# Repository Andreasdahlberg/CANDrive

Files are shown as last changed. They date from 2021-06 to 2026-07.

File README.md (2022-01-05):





# CANDrive
CANDrive is a brushed DC Motor Controller controlled via a [CAN](https://en.wikipedia.org/wiki/CAN_bus) interface.

## Features

* Velocity control
* Torque control
* CAN interface
* Firmware updates over CAN
* Emergency stop
* 5 A output current
* 12-24 V supply voltage

## Getting started

### Getting the Source

This project is [hosted on GitHub](https://github.com/Andreasdahlberg/CANDrive). You can clone this project directly using this command:

```
git clone --recurse-submodules https://github.com/Andreasdahlberg/CANDrive.git
```

### Building

```
scons build-opencm
scons build
```

### Running Tests

Run all tests with valgrind:
```
scons test
```

Run a single test suite:
```
scons app/motor/test && build/motor/test/TestRunner
```

Run a single unit test:
```
scons app/motor/test && build/motor/test/TestRunner test_Motor_SetSpeed
```

### Tools

#### Monitor
The monitor tool is a serial terminal which parses serial output from the device and formats the
output to make it easier to read. It also incorporates a simple command line used for debug commands 
and device configuration. The debug commands are not intended for controlling the motors during normal 
operation since they bypass several of the safety features.

##### Features
* Host timestamps
* Color coded debug levels
* Translation from addresses to file and line
* Command line
* Filtering[Not implemented]

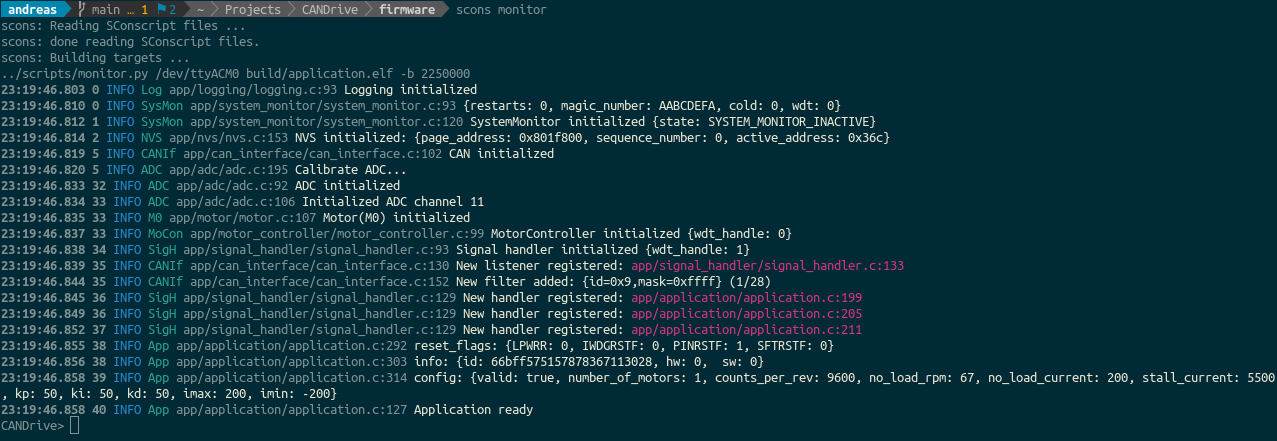
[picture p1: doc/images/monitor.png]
Example of monitor output


##### Usage
The monitor is started by typing *scons monitor*.
Serial port and baudrate can be configured [here](firmware/config.py) or on the command line, e.g.
*scons monitor SERIAL_PORT=/dev/ttyACM0 BAUD_RATE=921600*

The serial port used by the monitor is available at JP1 and is disabled by default. It can be 
enabled by moving jumper J1.

##### Available commands
###### rpm
rpm \[MOTOR_INDEX\] \[RPM\]

Ex.
```
CANDrive> rpm 0 50
```

###### current
current \[MOTOR_INDEX\] \[CURRENT\]

Ex.
```
CANDrive> current 1 1500
```

###### run
run \[MOTOR_INDEX\]

Ex.
```
CANDrive> run 0
```

###### coast
coast \[MOTOR_INDEX\]

Ex.
```
CANDrive> coast 0
```

###### brake
brake \[MOTOR_INDEX\]

Ex.
```
CANDrive> brake 0
```

###### reset
reset

Ex.
```
CANDrive> reset
```

###### level
level \[MODULE\] \[LEVEL\]

Ex.
```
CANDrive> level App 10
```

###### store
store \[PARAMETER\] \[VALUE\]

Ex.
```
CANDrive> store number_of_motors 1
```

## Hardware
[BOM](https://octopart.com/bom-tool/TDnAzRKf)

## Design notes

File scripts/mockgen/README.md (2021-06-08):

# Mock generator
This is a script for generating mock functions from header files for use with
the [cmocka](https://cmocka.org/) unit testing framework.

**This is a quick hack right now!**

## Usage
Generate mock functions and save to file
```bash
$ ./mockgen.py HEADER TEMPLATE > mock.c
```

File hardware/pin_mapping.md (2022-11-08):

# Pin Mapping

| PIN  | Name | Note |
|---|---|---|
| PC8  | PWM_1  | PWM signal for motor 1. |
| PC0  | SEL_1  | Current sense/diag selection. |
| PC1  | CS_1 | Current sense for motor 1. |
| PC2  | INA_1  | Output A for motor 1. |
| PC3  | INB_1  | Output B for motor 1. |
| PB6  | ENCA_1 | Encoder input A for motor 1.  |
| PB7  | ENCB_1 | Encoder input B for motor 1.  |
| PC6  | PWM_2  | PWM signal for motor 2. |
| PB13 | SEL_2  | Current sense/diag selection. |
| PB1  | CS_2 | Current sense for motor 2. |
| PB14 | INA_2  | Output A for motor 2. |
| PB15 | INB_2  | Output B for motor 2. |
| PA0  | ENCA_2 | Encoder input A for motor 2.  |
| PA1  | ENCB_2 | Encoder input B for motor 2.  |
| PA5  | LED_1  | Device status LED. |
| PC13 | ESTOP  | Emergency stop. |
| PA2  | USART_TX  | USART TX |
| PA3  | USART_RX  | USART RX |
| PA11 | CAN_RX  | CAN RX |
| PA12 | CAN_TX  | CAN TX |
| PC4  | VSENSE  | Battery voltage |

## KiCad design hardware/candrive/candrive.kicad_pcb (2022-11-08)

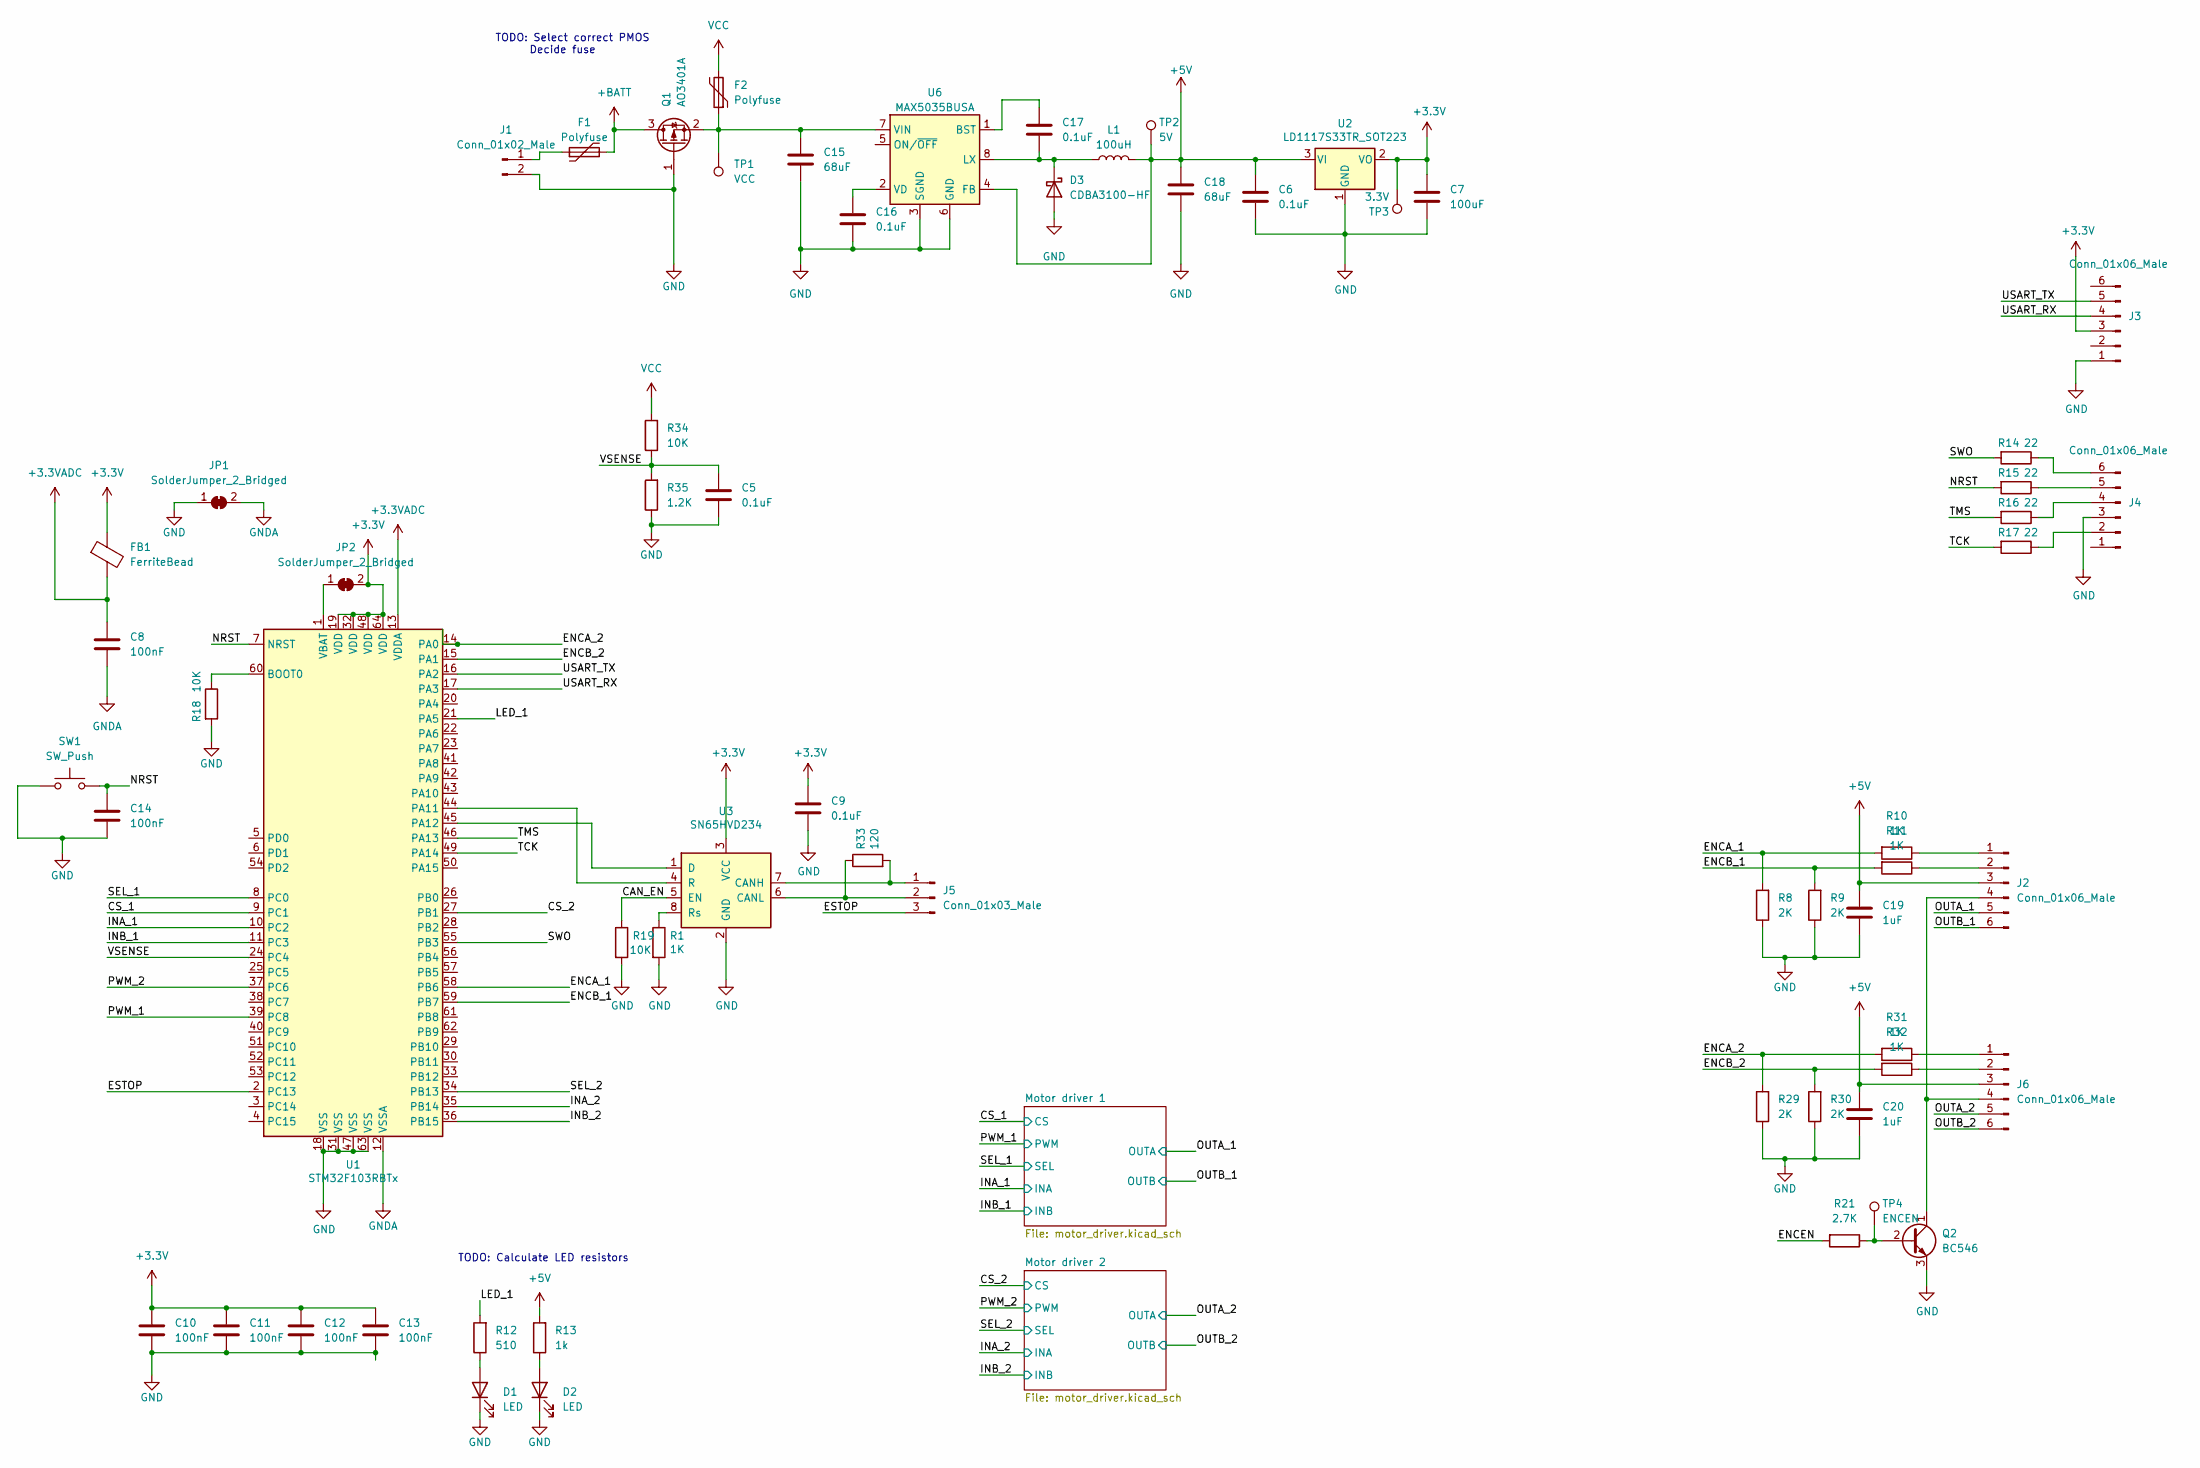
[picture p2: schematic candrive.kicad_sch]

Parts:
C5, C6, C9, C16, C17: 0.1uF; C_0805_2012Metric_Pad1.18x1.45mm_HandSolder
C7: 100uF; C_0805_2012Metric_Pad1.18x1.45mm_HandSolder
C8, C10, C11, C12, C13, C14: 100nF; C_0805_2012Metric_Pad1.18x1.45mm_HandSolder
C15, C18: 68uF; C_0805_2012Metric_Pad1.18x1.45mm_HandSolder
C19, C20: 1uF; C_0805_2012Metric_Pad1.18x1.45mm_HandSolder
D1, D2: LED; LED_0805_2012Metric_Pad1.15x1.40mm_HandSolder
D3: CDBA3100-HF; D_SMA
F1, F2: Polyfuse; Fuse_Bourns_MF-RHT300
FB1: FerriteBead; LairdTech_28C0236-0JW-10
J1: Conn_01x02_Male; PinHeader_1x02_P2.54mm_Horizontal
J2, J6: Conn_01x06_Male; PinHeader_1x06_P2.54mm_Horizontal
J3, J4: Conn_01x06_Male; PinHeader_1x06_P2.54mm_Vertical
J5: Conn_01x03_Male; PinHeader_1x03_P2.54mm_Horizontal
JP1, JP2: SolderJumper_2_Bridged; SolderJumper-2_P1.3mm_Open_TrianglePad1.0x1.5mm
L1: 100uH; L_0805_2012Metric_Pad1.05x1.20mm_HandSolder
Q1: AO3401A; SOT-23
Q2: BC546; TO-92_Inline
R1, R10, R11, R31, R32: 1K; R_0805_2012Metric_Pad1.20x1.40mm_HandSolder
R8, R9, R29, R30: 2K; R_0805_2012Metric_Pad1.20x1.40mm_HandSolder
R12: 510; R_0805_2012Metric_Pad1.20x1.40mm_HandSolder
R13: 1k; R_0805_2012Metric_Pad1.20x1.40mm_HandSolder
R14, R15, R16, R17: 22; R_0805_2012Metric_Pad1.20x1.40mm_HandSolder
R18, R19, R34: 10K; R_0805_2012Metric_Pad1.20x1.40mm_HandSolder
R21: 2.7K; R_0805_2012Metric_Pad1.20x1.40mm_HandSolder
R33: 120; R_0805_2012Metric_Pad1.20x1.40mm_HandSolder
R35: 1.2K; R_0805_2012Metric_Pad1.20x1.40mm_HandSolder
SW1: SW_Push; SW_Push_1P1T_NO_CK_KSC6xxJ
TP1: VCC; TestPoint_THTPad_D1.0mm_Drill0.5mm
TP2: 5V; TestPoint_THTPad_D1.0mm_Drill0.5mm
TP3: 3.3V; TestPoint_THTPad_D1.0mm_Drill0.5mm
TP4: ENCEN; TestPoint_THTPad_D1.0mm_Drill0.5mm
U1: STM32F103RBTx; LQFP-64_10x10mm_P0.5mm
U2: LD1117S33TR_SOT223; SOT-223-3_TabPin2
U3: SN65HVD234; SOIC-8_3.9x4.9mm_P1.27mm
U6: MAX5035BUSA; SOIC-8_3.9x4.9mm_P1.27mm

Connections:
+3.3VADC: C8.1, FB1.2, U1.13 (VDDA)
+3V3: C7.1, C9.1, C10.1, C11.1, C12.1, C13.1, FB1.1, J3.3, JP2.2 (B), TP3.1, U1.19 (VDD), U1.32 (VDD), U1.48 (VDD), U1.64 (VDD), U2.2 (VO), U3.3 (VCC)
+5V: C6.1, C18.1, C19.1, C20.1, J2.3, J6.3, L1.2, R13.2, TP2.1, U2.3 (VI), U6.4 (FB)
+BATT: F1.2, Q1.3 (D)
/CAN_EN: R19.1, U3.5 (EN)
/CS_1: U1.9 (PC1); also elsewhere on the board
/CS_2: U1.27 (PB1); also elsewhere on the board
/ENCA_1: R8.2, R10.2, U1.58 (PB6)
/ENCA_2: R29.2, R31.2, U1.14 (PA0)
/ENCB_1: R9.2, R11.2, U1.59 (PB7)
/ENCB_2: R30.2, R32.2, U1.15 (PA1)
/ENCEN: R21.2
/ESTOP: J5.3, U1.2 (PC13)
/INA_1: U1.10 (PC2); also elsewhere on the board
/INA_2: U1.35 (PB14); also elsewhere on the board
/INB_1: U1.11 (PC3); also elsewhere on the board
/INB_2: U1.36 (PB15); also elsewhere on the board
/LED_1: R12.2, U1.21 (PA5)
/NRST: C14.1, R15.2, SW1.2, U1.7 (NRST)
/OUTA_1: J2.5; also elsewhere on the board
/OUTA_2: J6.5; also elsewhere on the board
/OUTB_1: J2.6; also elsewhere on the board
/OUTB_2: J6.6; also elsewhere on the board
/PWM_1: U1.39 (PC8); also elsewhere on the board
/PWM_2: U1.37 (PC6); also elsewhere on the board
/SEL_1: U1.8 (PC0); also elsewhere on the board
/SEL_2: U1.34 (PB13); also elsewhere on the board
/SWO: R14.2, U1.55 (PB3)
/TCK: R17.2, U1.49 (PA14)
/TMS: R16.2, U1.46 (PA13)
/USART_RX: J3.4, U1.17 (PA3)
/USART_TX: J3.5, U1.16 (PA2)
GND: C5.2, C6.2, C7.2, C9.2, C10.2, C11.2, C12.2, C13.2, C14.2, C15.2, C16.2, C18.2, C19.2, C20.2, D1.1 (K), D2.1 (K), D3.2 (A), J1.2, J3.1, J4.3, JP1.1 (A), Q1.1 (G), Q2.3 (E), R1.2, R8.1, R9.1, R18.2, R19.2, R29.1, R30.1, R35.1, SW1.1, U1.18 (VSS), U1.31 (VSS), U1.47 (VSS), U1.63 (VSS), U2.1 (GND), U3.2 (GND), U6.3 (SGND), U6.6 (GND); also elsewhere on the board
GNDA: C8.2, JP1.2 (B), U1.12 (VSSA)
unnamed: C5.1, R34.1, R35.2, U1.24 (PC4)
unnamed: C15.1, F2.1, Q1.2 (S), TP1.1, U6.7 (VIN)
unnamed: C16.1, U6.2 (VD)
unnamed: C17.1, U6.1 (BST)
unnamed: C17.2, D3.1 (K), L1.1, U6.8 (LX)
unnamed: D1.2 (A), R12.1
unnamed: D2.2 (A), R13.1
unnamed: F1.1, J1.1
unnamed: J2.1, R10.1
unnamed: J2.2, R11.1
unnamed: J2.4, J6.4, Q2.1 (C)
unnamed: J4.2, R17.1
unnamed: J4.4, R16.1
unnamed: J4.5, R15.1
unnamed: J4.6, R14.1
unnamed: J5.1, R33.2, U3.7 (CANH)
unnamed: J5.2, R33.1, U3.6 (CANL)
unnamed: J6.1, R31.1
unnamed: J6.2, R32.1
unnamed: JP2.1 (A), U1.1 (VBAT)
unnamed: Q2.2 (B), R21.1, TP4.1
unnamed: R1.1, U3.8 (Rs)
unnamed: R18.1, U1.60 (BOOT0)
unnamed: U1.44 (PA11), U3.4 (R)
unnamed: U1.45 (PA12), U3.1 (D)
VCC: F2.2, R34.2; also elsewhere on the board

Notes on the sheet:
TODO: Calculate LED resistors
TODO: Select correct PMOS Decide fuse

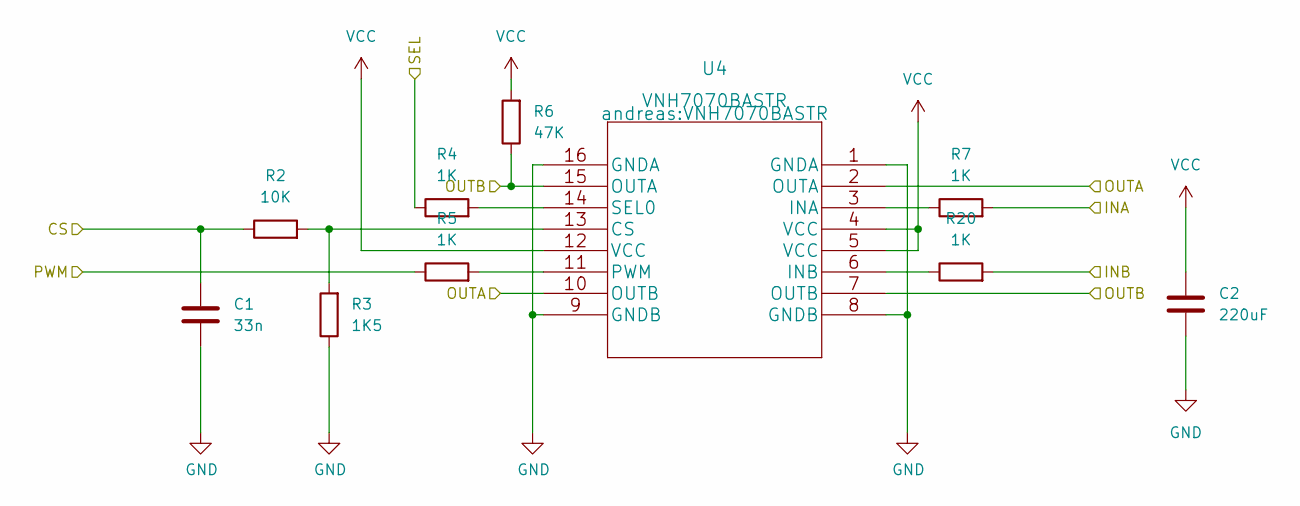
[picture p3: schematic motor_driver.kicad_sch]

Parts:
C1: 33n; C_0805_2012Metric_Pad1.18x1.45mm_HandSolder
C2: 220uF; C_0805_2012Metric_Pad1.18x1.45mm_HandSolder
R2: 10K; R_0805_2012Metric_Pad1.20x1.40mm_HandSolder
R3: 1K5; R_0805_2012Metric_Pad1.20x1.40mm_HandSolder
R4, R5, R7, R20: 1K; R_0805_2012Metric_Pad1.20x1.40mm_HandSolder
R6: 47K; R_0805_2012Metric_Pad1.20x1.40mm_HandSolder
U4: VNH7070BASTR

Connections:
/CS_1: C1.1, R2.1; also elsewhere on the board
/INA_1: R7.2; also elsewhere on the board
/INB_1: R20.2; also elsewhere on the board
/OUTA_1: U4.2 (OUTA), U4.10 (OUTB); also elsewhere on the board
/OUTB_1: R6.1, U4.7 (OUTB), U4.15 (OUTA); also elsewhere on the board
/PWM_1: R5.1; also elsewhere on the board
/SEL_1: R4.1; also elsewhere on the board
GND: C1.2, C2.2, R3.1, U4.1 (GNDA), U4.8 (GNDB), U4.9 (GNDB), U4.16 (GNDA); also elsewhere on the board
unnamed: R2.2, R3.2, U4.13 (CS)
unnamed: R4.2, U4.14 (SEL0)
unnamed: R5.2, U4.11 (PWM)
unnamed: R7.1, U4.3 (INA)
unnamed: R20.1, U4.6 (INB)
VCC: C2.1, R6.2, U4.4 (VCC), U4.5 (VCC), U4.12 (VCC); also elsewhere on the board

Board: 4 copper layers, 80 parts (0 on the bottom side), 68 nets, no tracks yet.

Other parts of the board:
C3: 33n; C_0805_2012Metric_Pad1.18x1.45mm_HandSolder
C4: 220uF; C_0805_2012Metric_Pad1.18x1.45mm_HandSolder
R22: 10K; R_0805_2012Metric_Pad1.20x1.40mm_HandSolder
R23: 1K5; R_0805_2012Metric_Pad1.20x1.40mm_HandSolder
R24, R25, R27, R28: 1K; R_0805_2012Metric_Pad1.20x1.40mm_HandSolder
R26: 47K; R_0805_2012Metric_Pad1.20x1.40mm_HandSolder
U5: VNH7070BASTR

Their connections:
/CS_2: C3.1, R22.1; also elsewhere on the board
/INA_2: R27.2; also elsewhere on the board
/INB_2: R28.2; also elsewhere on the board
/OUTA_2: U5.2 (OUTA), U5.10 (OUTB); also elsewhere on the board
/OUTB_2: R26.1, U5.7 (OUTB), U5.15 (OUTA); also elsewhere on the board
/PWM_2: R25.1; also elsewhere on the board
/SEL_2: R24.1; also elsewhere on the board
GND: C3.2, C4.2, R23.1, U5.1 (GNDA), U5.8 (GNDB), U5.9 (GNDB), U5.16 (GNDA); also elsewhere on the board
unnamed: R22.2, R23.2, U5.13 (CS)
unnamed: R24.2, U5.14 (SEL0)
unnamed: R25.2, U5.11 (PWM)
unnamed: R27.1, U5.3 (INA)
unnamed: R28.1, U5.6 (INB)
VCC: C4.1, R26.2, U5.4 (VCC), U5.5 (VCC), U5.12 (VCC); also elsewhere on the board

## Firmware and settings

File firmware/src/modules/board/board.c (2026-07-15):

/**
 * @file   board.c
 * @Author Andreas Dahlberg (andreas.dahlberg90@gmail.com)
 * @brief  Board support module.
 */

/*
This file is part of CANDrive firmware.

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
You should have received a copy of the GNU General Public License
along with CANDrive firmware.  If not, see <http://www.gnu.org/licenses/>.
*/

//////////////////////////////////////////////////////////////////////////
//INCLUDES
//////////////////////////////////////////////////////////////////////////

#include <libopencm3/stm32/timer.h>
#include <libopencm3/stm32/rcc.h>
#include <libopencm3/cm3/common.h>
#include <libopencm3/stm32/gpio.h>
#include <libopencm3/cm3/scb.h>
#include <stdint.h>
#include <assert.h>
#include "memory_map.h"
#include "utility.h"
#include "board.h"

//////////////////////////////////////////////////////////////////////////
//DEFINES
//////////////////////////////////////////////////////////////////////////

#define NUMBER_OF_MOTORS 2
#define GPIO_STATUS_LED_CLOCK RCC_GPIOA
#define GPIO_STATUS_LED_PORT GPIOA
#define GPIO_STATUS_LED GPIO5
#define GPIO_EMERGENCY_CLOCK RCC_GPIOC
#define GPIO_EMERGENCY_PORT GPIOC
#define GPIO_EMERGENCY GPIO13

//////////////////////////////////////////////////////////////////////////
//TYPE DEFINITIONS
//////////////////////////////////////////////////////////////////////////

struct module_t
{
    const struct board_motor_config_t motor_configs[NUMBER_OF_MOTORS];
    uint32_t reset_flags;
};

//////////////////////////////////////////////////////////////////////////
//VARIABLES
//////////////////////////////////////////////////////////////////////////

static struct module_t module =
{
    .motor_configs = {
        {
            .pwm = {
                .timer_peripheral = TIM3,
                .remap = AFIO_MAPR_TIM3_REMAP_FULL_REMAP,
                .gpio_port = GPIOC,
                .gpio = GPIO8,
                .oc_id = TIM_OC3,
                .peripheral_clocks = {RCC_GPIOC, RCC_TIM3, RCC_AFIO}
            },
            .driver = {
                .port = GPIOC,
                .sel = GPIO0,
                .cs = GPIO1,
                .ina = GPIO2,
                .inb = GPIO3,
                .gpio_clock = RCC_GPIOC
            },
            .encoder = {
                .port = GPIOB,
                .a = GPIO6,
                .b = GPIO7,
                .gpio_clock = RCC_GPIOB,
                .timer = TIM4,
                .timer_clock = RCC_TIM4,
                .timer_rst = RST_TIM4
            },
            .adc = {
                .channel = 11
            }
        },
        {
            .pwm = {
                .timer_peripheral = TIM3,
                .remap = AFIO_MAPR_TIM3_REMAP_FULL_REMAP,
                .gpio_port = GPIOC,
                .gpio = GPIO6,
                .oc_id = TIM_OC1,
                .peripheral_clocks = {RCC_GPIOC, RCC_TIM3, RCC_AFIO}
            },
            .driver = {
                .port = GPIOB,
                .sel = GPIO13,
                .cs = GPIO1,
                .ina = GPIO14,
                .inb = GPIO15,
                .gpio_clock = RCC_GPIOB
            },
            .encoder = {
                .port = GPIOA,
                .a = GPIO0,
                .b = GPIO1,
                .gpio_clock = RCC_GPIOA,
                .timer = TIM2,
                .timer_clock = RCC_TIM2,
                .timer_rst = RST_TIM2
            },
            .adc = {
                .channel = 9
            }
        }
    },
    0
};

//////////////////////////////////////////////////////////////////////////
//LOCAL FUNCTION PROTOTYPES
//////////////////////////////////////////////////////////////////////////

static void StoreResetFlags(void);
static void ClearResetFlags(void);
static void SetupClock(void);
static void SetupGPIO(void);

//////////////////////////////////////////////////////////////////////////
//FUNCTIONS
//////////////////////////////////////////////////////////////////////////

void Board_Init(void)
{
    StoreResetFlags();
    ClearResetFlags();
    SetupClock();
    SetupGPIO();
}

uint32_t Board_GetHardwareRevision(void)
{
    return 0;
}

uint32_t Board_GetSoftwareRevision(void)
{
    return 0;
}

struct board_id_t Board_GetId(void)
{
    const uintptr_t uid_base_address = 0x1FFFF7E8;

    struct board_id_t id;
    id.offset_0 = MMIO32(uid_base_address);
    id.offset_4 = MMIO32(uid_base_address + 4);
    id.offset_8 = MMIO32(uid_base_address + 8);

    return id;
}

const struct board_motor_config_t *Board_GetMotorConfig(size_t index)
{
    assert(index < ElementsIn(module.motor_configs));

    return &module.motor_configs[index];
}

size_t Board_GetMaxNumberOfMotors(void)
{
    return ElementsIn(module.motor_configs);
}

void Board_ToggleStatusLED(void)
{
    gpio_toggle(GPIO_STATUS_LED_PORT, GPIO_STATUS_LED);
}

uint32_t Board_GetResetFlags(void)
{
    return module.reset_flags;
}

void Board_Reset(void)
{
    scb_reset_system();
}
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

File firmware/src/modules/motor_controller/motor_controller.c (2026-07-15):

/**
 * @file   motor_controller.c
 * @Author Andreas Dahlberg (andreas.dahlberg90@gmail.com)
 * @brief  Motor manager module.
 */

/*
This file is part of CANDrive firmware.

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
You should have received a copy of the GNU General Public License
along with CANDrive firmware.  If not, see <http://www.gnu.org/licenses/>.
*/

//////////////////////////////////////////////////////////////////////////
//INCLUDES
//////////////////////////////////////////////////////////////////////////

#include <assert.h>
#include <stdio.h>
#include <stdlib.h>
#include <inttypes.h>
#include "utility.h"
#include "logging.h"
#include "board.h"
#include "config.h"
#include "systime.h"
#include "pid.h"
#include "system_monitor.h"
#include "motor_controller.h"

//////////////////////////////////////////////////////////////////////////
//DEFINES
//////////////////////////////////////////////////////////////////////////

#define MOTOR_CONTROLLER_LOGGER_NAME "MoCon"
#ifndef MOTOR_CONTROLLER_LOGGER_DEBUG_LEVEL
#define MOTOR_CONTROLLER_LOGGER_DEBUG_LEVEL LOGGING_INFO
#endif

#define MAX_NUMBER_OF_MOTORS 2
#define UPDATE_TIME_MS 10
#define PID_SCALE 10
#define PID_CV_MAX 1000
#define PID_CV_MIN (-PID_CV_MAX)

//////////////////////////////////////////////////////////////////////////
//TYPE DEFINITIONS
//////////////////////////////////////////////////////////////////////////

struct motor_instance_t
{
    struct motor_t motor;
    struct pid_t rpm_pid;
    struct pid_t current_pid;
};

struct motor_controller_t
{
    logging_logger_t *logger_p;
    struct motor_instance_t instances[MAX_NUMBER_OF_MOTORS];
    uint32_t update_time;
    uint32_t watchdog_handle;
};

//////////////////////////////////////////////////////////////////////////
//VARIABLES
//////////////////////////////////////////////////////////////////////////

static struct motor_controller_t module;

//////////////////////////////////////////////////////////////////////////
//LOCAL FUNCTION PROTOTYPES
//////////////////////////////////////////////////////////////////////////

static inline void InitializeMotors(void);
static inline void UpdateMotors(void);
static inline void UpdateMotorSpeeds(void);
static void ResetPIDControllers(struct motor_instance_t *instance_p);
static int32_t LimitValue(int32_t value, int32_t min, int32_t max);
static void UpdateCVLimits(struct pid_parameters_t *parameters_p, int32_t sp);

//////////////////////////////////////////////////////////////////////////
//FUNCTIONS
//////////////////////////////////////////////////////////////////////////

void MotorController_Init(void)
{
    module = (__typeof__(module)) {0};
    module.watchdog_handle = SystemMonitor_GetWatchdogHandle();
    module.logger_p = Logging_GetLogger(MOTOR_CONTROLLER_LOGGER_NAME);
    Logging_SetLevel(module.logger_p, MOTOR_CONTROLLER_LOGGER_DEBUG_LEVEL);

    InitializeMotors();
    Logging_Info(module.logger_p, "MotorController initialized {wdt_handle: %u}",
                 module.watchdog_handle);
}

void MotorController_Update(void)
{
    UpdateMotors();

    if (SysTime_GetDifference(module.update_time) >= UPDATE_TIME_MS)
    {
        UpdateMotorSpeeds();
        SystemMonitor_FeedWatchdog(module.watchdog_handle);
        module.update_time = SysTime_GetSystemTime();
    }
}

void MotorController_SetRPM(size_t index, int16_t rpm)
{
    assert(index < Config_GetNumberOfMotors());

    const int32_t max_rpm = (int32_t)Config_GetNoLoadRpm();
    const int32_t min_rpm = max_rpm * -1;
    const int32_t limited_rpm = LimitValue(rpm, min_rpm, max_rpm);

    /**
     * Limit the control value in one direction to prevent driving the motor in
     * the opposite direction when decreasing/increasing the RPM.
     */
    UpdateCVLimits(PID_GetParameters(&module.instances[index].rpm_pid), limited_rpm);
    UpdateCVLimits(PID_GetParameters(&module.instances[index].current_pid), limited_rpm);

    PID_SetSetpoint(&module.instances[index].rpm_pid, limited_rpm);
    Logging_Debug(module.logger_p, "M%u sp: {rpm: %i}", index, limited_rpm);
}

void MotorController_SetCurrent(size_t index, int16_t current)
{
    assert(index < Config_GetNumberOfMotors());

    const uint32_t max_board_current = Board_GetMaxCurrent();
    const uint32_t stall_current = Config_GetStallCurrent();
    const int32_t max_current = (max_board_current < stall_current) ? (int32_t)max_board_current : (int32_t)stall_current;
    const int32_t min_current = max_current * -1;
    const int32_t limited_current = LimitValue(current, min_current, max_current);

    PID_SetSetpoint(&module.instances[index].current_pid, limited_current);
    Logging_Debug(module.logger_p, "M%u sp: {current: %i}", index, limited_current);
}

void MotorController_Run(size_t index)
{
    assert(index < Config_GetNumberOfMotors());
    if (Motor_GetStatus(&module.instances[index].motor) != MOTOR_RUN)
    {
        Motor_SetSpeed(&module.instances[index].motor, 0);
    }
}

void MotorController_Coast(size_t index)
{
    assert(index < Config_GetNumberOfMotors());
    if (Motor_GetStatus(&module.instances[index].motor) != MOTOR_COAST)
    {
        Motor_Coast(&module.instances[index].motor);
        ResetPIDControllers(&module.instances[index]);
    }
}

void MotorController_Brake(size_t index)
{
    assert(index < Config_GetNumberOfMotors());
    if (Motor_GetStatus(&module.instances[index].motor) != MOTOR_BRAKE)
    {
        Motor_Brake(&module.instances[index].motor);
        ResetPIDControllers(&module.instances[index]);
    }
}

uint32_t MotorController_GetPosition(size_t index)
{
    assert(index < Config_GetNumberOfMotors());

    return Motor_GetPosition(&module.instances[index].motor);
}

struct motor_controller_motor_status_t MotorController_GetStatus(size_t index)
{
    assert(index < Config_GetNumberOfMotors());

    const struct motor_instance_t *instance_p = &module.instances[index];
    struct motor_controller_motor_status_t status;
    status.rpm.actual = Motor_GetRPM(&instance_p->motor);
    status.rpm.target = (int16_t)PID_GetSetpoint(&instance_p->rpm_pid);
    status.current.actual = Motor_GetCurrent(&instance_p->motor);
    status.current.target = (int16_t)PID_GetSetpoint(&instance_p->current_pid);
    status.status = Motor_GetStatus(&instance_p->motor);

    return status;
}

//////////////////////////////////////////////////////////////////////////
//LOCAL FUNCTIONS
//////////////////////////////////////////////////////////////////////////
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

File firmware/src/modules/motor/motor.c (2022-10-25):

/**
 * @file   motor.c
 * @Author Andreas Dahlberg (andreas.dahlberg90@gmail.com)
 * @brief  Motor module.
 */

/*
This file is part of CANDrive firmware.

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
You should have received a copy of the GNU General Public License
along with CANDrive firmware.  If not, see <http://www.gnu.org/licenses/>.
*/

//////////////////////////////////////////////////////////////////////////
//INCLUDES
//////////////////////////////////////////////////////////////////////////

#include <libopencm3/stm32/rcc.h>
#include <libopencm3/stm32/gpio.h>
#include <libopencm3/stm32/timer.h>
#include <libopencm3/cm3/nvic.h>
#include <assert.h>
#include <stdlib.h>
#include "utility.h"
#include "systime.h"
#include "config.h"
#include "motor.h"

//////////////////////////////////////////////////////////////////////////
//DEFINES
//////////////////////////////////////////////////////////////////////////

#ifndef MOTOR_LOGGER_DEBUG_LEVEL
#define MOTOR_LOGGER_DEBUG_LEVEL LOGGING_INFO
#endif

//////////////////////////////////////////////////////////////////////////
//TYPE DEFINITIONS
//////////////////////////////////////////////////////////////////////////

//////////////////////////////////////////////////////////////////////////
//VARIABLES
//////////////////////////////////////////////////////////////////////////

static const uint32_t PWM_FREQUENCY = 20000;
static const uint32_t SAMPLE_FREQUENCY_HZ = 100;

//////////////////////////////////////////////////////////////////////////
//LOCAL FUNCTION PROTOTYPES
//////////////////////////////////////////////////////////////////////////

static inline void SetupGPIO(const struct motor_t *self_p);
static inline void SetupTimer(const struct motor_t *self_p);
static inline uint16_t SpeedToDutyCycle(int16_t speed);
static inline void SetGpio(const struct motor_t *self_p, uint16_t gpio, bool state);
static inline void SetDirection(struct motor_t *self_p);
static inline uint32_t GetPosition(const struct motor_t *self_p);
static inline void ResetPosition(const struct motor_t *self_p);
static inline int16_t SenseVoltageToCurrent(const struct motor_t *self_p, uint32_t sense_voltage);
static inline int32_t GetCountDifference(const struct motor_t *self_p, int32_t count);
static inline int32_t CountToRPM(const struct motor_t *self_p, int32_t count, uint32_t frequency);
static inline void UpdateCurrentVoltageFilter(struct motor_t *self_p);

//////////////////////////////////////////////////////////////////////////
//FUNCTIONS
//////////////////////////////////////////////////////////////////////////

void Motor_Init(struct motor_t *self_p,
                const char *name,
                const struct board_motor_config_t *config_p)
{
    assert(self_p != NULL);
    assert(name != NULL);
    assert(config_p != NULL);

    *self_p = (__typeof__(*self_p)) {0};
    self_p->config_p = config_p;
    self_p->status = MOTOR_RUN;
    self_p->counts_per_revolution = (int32_t)Config_GetCountsPerRev();
    assert(self_p->counts_per_revolution > 0);

    self_p->logger_p = Logging_GetLogger(name);
    Logging_SetLevel(self_p->logger_p, MOTOR_LOGGER_DEBUG_LEVEL);

    SetupGPIO(self_p);
    SetupTimer(self_p);

    ResetPosition(self_p);

    ADC_InitChannel(&self_p->adc_input, self_p->config_p->adc.channel);

    PWM_Init(&self_p->pwm_output, &config_p->pwm);
    PWM_Disable(&self_p->pwm_output);
    PWM_SetFrequency(&self_p->pwm_output, PWM_FREQUENCY);
    PWM_SetDuty(&self_p->pwm_output, 0);

    Logging_Info(self_p->logger_p, "Motor(%s) initialized", name);
}

void Motor_Update(struct motor_t *self_p)
{
    assert(self_p != NULL);
    const uint32_t update_period_ms = 1000 / SAMPLE_FREQUENCY_HZ;

    const uint32_t time_since_last_update = SysTime_GetDifference(self_p->timer);
    if (time_since_last_update >= update_period_ms)
    {
        const int32_t count = (int32_t)GetPosition(self_p);
        const int32_t difference = GetCountDifference(self_p, count);
        const uint32_t actual_sample_frequency = 1000 / time_since_last_update;
        self_p->rpm = (int16_t)CountToRPM(self_p, difference, actual_sample_frequency);
        self_p->count = count;

        UpdateCurrentVoltageFilter(self_p);

        self_p->timer = SysTime_GetSystemTime();
    }
}

int16_t Motor_GetRPM(const struct motor_t *self_p)
{
    assert(self_p != NULL);
    return self_p->rpm;
}

int16_t Motor_GetCurrent(const struct motor_t *self_p)
{
    assert(self_p != NULL);

    return SenseVoltageToCurrent(self_p, Filter_Output(&self_p->filter));
}

void Motor_SetSpeed(struct motor_t *self_p, int16_t speed)
{
    assert(self_p != NULL);
    assert(speed >= -1000 && speed <= 1000);

    if ((self_p->status != MOTOR_RUN) || (speed != self_p->speed))
    {
        self_p->speed = speed;
        const uint16_t duty_cycle = SpeedToDutyCycle(speed);

        PWM_Disable(&self_p->pwm_output);
        SetDirection(self_p);
        PWM_SetDuty(&self_p->pwm_output, duty_cycle);
        PWM_Enable(&self_p->pwm_output);

        self_p->status = MOTOR_RUN;
        Logging_Debug(self_p->logger_p, "{rpm: % i, speed: %i}", self_p->rpm, speed);
    }
}

void Motor_Coast(struct motor_t *self_p)
{
    assert(self_p != NULL);

    PWM_SetDuty(&self_p->pwm_output, 0);
    self_p->status = MOTOR_COAST;

    Logging_Info(self_p->logger_p, "Coasting enabled");
}

void Motor_Brake(struct motor_t *self_p)
{
    assert(self_p != NULL);

    PWM_Disable(&self_p->pwm_output);

    SetGpio(self_p, self_p->config_p->driver.ina, false);
    SetGpio(self_p, self_p->config_p->driver.inb, false);

    const uint32_t max_duty = 1000;
    PWM_SetDuty(&self_p->pwm_output, max_duty);
    PWM_Enable(&self_p->pwm_output);
    self_p->status = MOTOR_BRAKE;

    Logging_Info(self_p->logger_p, "Braking enabled");
}

enum motor_status_t Motor_GetStatus(const struct motor_t *self_p)
{
    assert(self_p != NULL);
    return self_p->status;
}

enum motor_direction_t Motor_GetDirection(const struct motor_t *self_p)
{
    assert(self_p != NULL);
    return self_p->direction;
}

uint32_t Motor_GetPosition(const struct motor_t *self_p)
{
    assert(self_p != NULL);
    return (GetPosition(self_p) * 360) / (uint32_t)self_p->counts_per_revolution;
}

const char *Motor_DirectionToString(const struct motor_t *self_p, enum motor_direction_t direction)
{
    assert(self_p != NULL);

    switch (direction)
    {
        case MOTOR_DIR_CW:
            return STRINGIFY(MOTOR_DIR_CW);
        case MOTOR_DIR_CCW:
            return STRINGIFY(MOTOR_DIR_CCW);
        default:
            Logging_Warning(self_p->logger_p, "Unknown direction: 0x%x", direction);
            return "UNKNOWN";
    }
}

//////////////////////////////////////////////////////////////////////////
//LOCAL FUNCTIONS
//////////////////////////////////////////////////////////////////////////
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

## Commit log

2021-03-07 Add KiCad project
    [candrive.kicad_pcb, candrive.sch]
2021-04-05 Add STM32F103 documentation
2021-05-18 Replace default hard fault handler
    The new fault handler inserts a breakpint if a debugger is connected.
2021-05-18 Switch to newlib-nano
2021-06-01 Enable Sonarcloud
2021-06-01 Update sonarcloud token
2021-06-03 Add sonarcloud badge to readme
2021-06-06 Update sonarcloud options
2021-06-08 Fix incorrect type conversion
    [can_interface.c]
2021-06-08 Replace register manipulation with libopencm3 function
    [can_interface.c]
2021-06-11 Add mock for the usart driver
2021-06-11 Fix incorrect printf format specifier
2021-06-14 Fix incorrect file documentation
    [can_interface.c]
2021-06-17 Update timer mock
2021-06-17 Implement PWM driver
2021-06-17 Add more PWM unit tests
2021-06-18 Only build libopencm3 for STM32F1
2021-06-18 Implement CAN ID filtering
2021-07-20 Implement motor module
2021-07-20 Update todo comment in motor module
2021-07-20 Implement PWM mock
2021-07-20 Add test skeleton for the motor module
2021-07-20 Add const to motor name argument
2021-07-20 Assert valid motor name
2021-07-20 Update PWM mock
2021-07-20 Implement unit test for 'Motor_Init()'
2021-07-20 Add more unit tests for the motor module
2021-07-20 Add encoder support to motor module
2021-07-20 Add more checks in timer mock
2021-07-20 Use 'timer_get_direction' instead of register access
2021-07-20 Add unit tests for motor module
2021-08-12 Add ADC module skeleton
2021-08-12 Implement prototype ADC driver
2021-08-12 Improve ADC module
2021-08-12 Add basic ADC mock
2021-08-12 Add basic DMA mock
2021-08-12 Add test structure for ADC
2021-08-12 Use define for DMA channel number
2021-08-12 Add function to get the ADC sample buffer
    This function is only available for unit tests. The correct way to get access
    to the sample buffer for testing should be via 'dma_set_memory_address()', but
    due to different pointer sizes on host and target this is not possible right now.
    [adc.c]
2021-08-12 Fix issue with incorrect values from ADC_GetVoltage()
    [adc.c]
2021-08-12 Update ADC and DMA mocks
2021-08-12 Cleanup ADC module
2021-08-12 Add more ADC unit tests
2021-08-12 Refactor ADC module
2021-08-15 Implement 'Motor_GetCurrent()'
2021-08-15 Add ADC mock
2021-08-17 Change CI-link in sonar project properties
2021-08-24 Add board module
2021-08-24 Use board module in main
2021-08-24 Add motor configuration to board module
2021-08-24 Use board configuration in PWM and motor module
2021-08-31 Implement EMA filter
2021-09-02 Fix issue with unintentional motor brake
    [motor.c]
2021-09-02 Implement function to get number of motors
2021-09-02 Implement PID controller
2021-09-02 Add unit test skeleton for the PID controller
2021-09-02 Add unit test for PID controller
2021-09-04 Use real values for motor encoder config
2021-09-14 Implement motor controller
2021-09-14 Only update motor speed if it has changed
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2021-09-14 Update motor unit test
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2021-09-14 Change max number of motors
2021-09-14 Add assert of pid parameter cvmax
2021-09-14 Implement unit tests for motor controller
2021-09-14 Add unit tests for motor controller commands
2021-09-14 Change default PID parameters
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2021-09-14 Implement coast/brake via motor controller
2021-09-14 Improve test coverage in 'Motor_SetSpeed'
2021-09-14 Add unit test for 'MotorController_Run'
2021-09-14 Integrate console and motor controller
2021-09-22 Move status LED control to 'Board'
2021-09-23 Implement function to get reset flags
    [board.c]
2021-09-24 Fix code smells
    Rename long function and fix implicit type cast.
    [board.c, signal_handler.c]
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2021-10-01 Decrease ADC calibration delay
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2021-10-18 Add null check in PID mock
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2021-10-18 Send motor status message
2021-10-28 Add second motor status to protocol
2021-10-28 Add second motor status to MOTOR_MSG_STATUS_FRAME
2021-10-28 Implement function to get emergency pin state
2021-11-29 Print failed asserts in monitor script
2021-11-29 Add NVS parameters to board module
2021-12-15 Add mode signal for both motors
2021-12-15 Remove max current from config
2021-12-15 Change motor status enum values
2021-12-15 Add test for configuration with no motors
2021-12-15 Add max number of motors and max current to board module
2021-12-15 Add motor status values to dbc file
2021-12-15 Add support for two motors in application
2021-12-15 Implement RPM and current limits
2021-12-15 Fix implicit type casts
    [motor.c]
2021-12-23 Add PID parameters to config
2021-12-23 Use PID parameters from config
2021-12-23 Add PID parameters to config dump
2021-12-23 Fix implicit type conversions
    [motor_controller.c]
2021-12-23 Fix sonar bug
2021-12-29 Add missing test to PID test runner
2021-12-29 Add imin and cvmin parameters in PID controller
2021-12-29 Set imin and cvmin in motor controller
2021-12-29 Implement support for running motor in reverse
    [motor.c]
2021-12-29 Improve test coverage in motor module
2021-12-29 Only brake/coast if not braking/coasting
2021-12-29 Update board info logging format
2022-01-01 Implement prototype python interface for candrive
2022-01-01 Print git version at start
2022-01-03 Fix issue with rpm spikes at low speeds
    [motor.c]
2022-01-05 Fix issue with incorrect rpm at fast motor acceleration
    Caused by voltage drop and noise on the encoder signals. Fixed
    by enabling input capture filtering. This might need some tweaking
    later on when running on the real hardware.
    [motor.c]
2022-01-05 Eliminate derivative kick in PID controller
2022-01-05 Improve precision when scaling cv in PID controller
2022-01-05 Increase motor pid/speed update frequency
2022-01-05 Fix issue with changing polarity when decreasing speed
    [motor_controller.c]
2022-01-15 Fix issue with full frame buffer in signal handler
    Caused by ISO-TP frames pushed to the signal handler frame buffer.
    [signal_handler.c]
2022-01-15 Remove unused function prototype
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2022-01-17 Fix issue with incorrect ISO-TP frame order
    [can_interface.c]
2022-01-18 Rearange includes in the board module
2022-01-18 Add unit tests for the board module
2022-02-09 Fix broken restart loop detection
    Use backup registers instead of RAM to store restart information.
    [system_monitor.c]
2022-02-09 Add monitor script to configure a device
2022-02-09 Fix issue with incorrect RPM during high CPU load
    [motor.c]
2022-02-09 Update device configuration script
2022-02-17 Fix issue with failed CAN transmit
    This might need some more work, maybe use a tx fifo and interrupts
    instead of a blocking wait.
    [can_interface.c]
2022-02-18 Configure sonarcloud test execution settings
2022-03-27 Remove support for two different app slots
2022-06-14 Fix missing and unused includes
    [serial.c]
2022-06-14 Print build ID at start
2022-06-14 Print image type in bootloader
2022-06-14 Move motor config to board module
2022-06-14 Fix broken motor controller test suite
2022-06-17 Implement status LED in the bootloader
2022-07-29 Fix incorrect bit mask in ADC driver
    [adc.c]
2022-08-05 Start ADC conversions at start up
2022-08-05 Add filter to motor current readings
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2022-08-07 Fix broken current control
    [motor_controller.c]
2022-10-25 Fix incorrect usage of GPIO remap function
    [pwm.c]
2022-10-25 Improve logging when using two motors
2022-10-25 Add configuration for second motor
2022-11-08 Update device schematic
    [candrive.kicad_pcb, candrive.kicad_sch, motor_driver.kicad_sch]
2022-11-20 Exclude third party code from sonarscan
2022-11-20 Implement a device monitoring wrapper
2022-11-20 Add missing mock return value
    [can_interface.c]
2022-11-20 Update device monitoring mock
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2022-11-20 Add unit tests device monitoring
2022-11-20 Handle ISOTP errors in device monitoring transport layer
2022-11-20 Improve error handling in device monitoring transport layer

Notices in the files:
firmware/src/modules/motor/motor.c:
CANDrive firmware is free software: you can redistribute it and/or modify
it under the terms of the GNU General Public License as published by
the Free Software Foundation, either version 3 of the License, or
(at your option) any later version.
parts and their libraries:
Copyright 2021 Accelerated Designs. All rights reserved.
